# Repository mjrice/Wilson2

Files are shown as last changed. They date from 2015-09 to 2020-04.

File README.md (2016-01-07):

# Wilson2

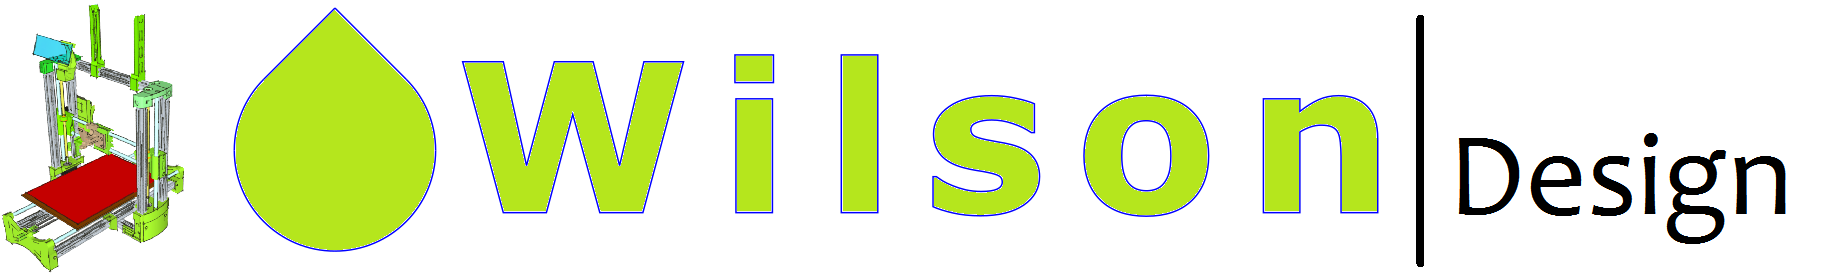
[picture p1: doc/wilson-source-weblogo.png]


This is the design repository for the Wilson II - a reprap 3D printer based on Wilson TS, inspired by the Prusa i3 and the Lulzbot TAZ.

The respository has these sub directories:

    stl/ contains the STL files needed to build the printer
    doc/ contains documentation, images, bom, etc.
    scad/ contains the design files of those parts for which OpenSCAD was used.
    sketchup/ contains the design files of those parts for which SketchUp was used.

There is also a community forum for this project, located at http://community.reprapwilson3d.com

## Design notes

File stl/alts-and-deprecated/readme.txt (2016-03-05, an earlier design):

/stl/alts-and-deprecated

The model files located in this folder are for 
rarely used alternate versions of some parts, or
deprecated models (things no longer recommended 
for the standard Wilson II build).

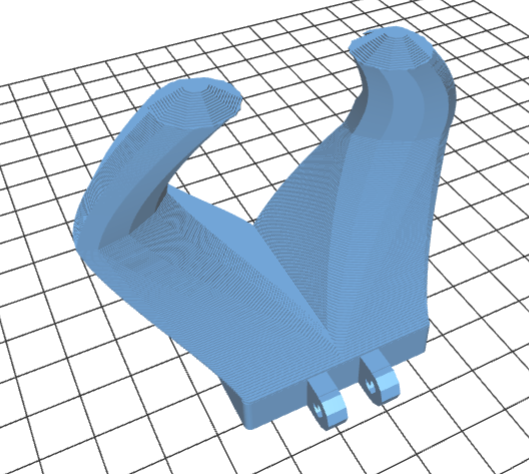
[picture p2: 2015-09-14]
doc/fanduct-e3dlite6.png

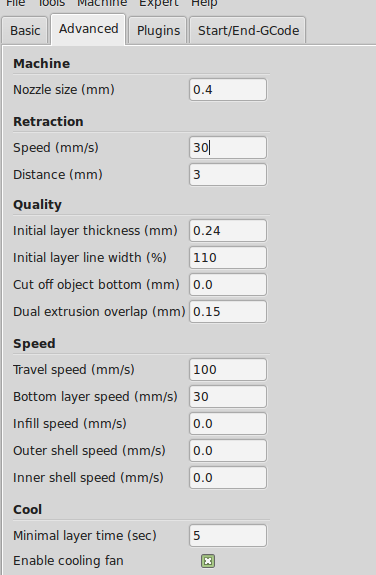
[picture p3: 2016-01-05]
doc/cura2.png

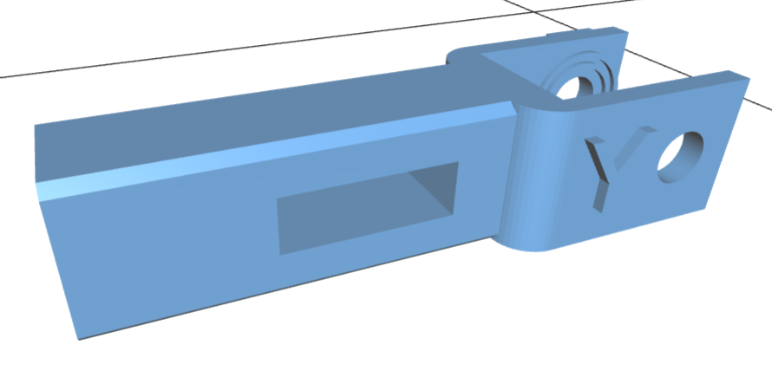
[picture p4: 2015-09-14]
doc/y-tensioner.png

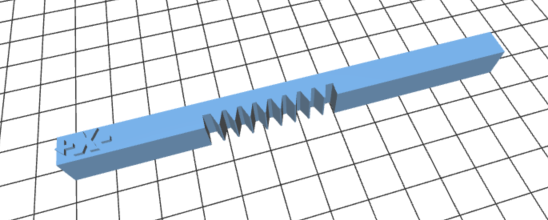
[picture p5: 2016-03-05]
doc/z-rack.png

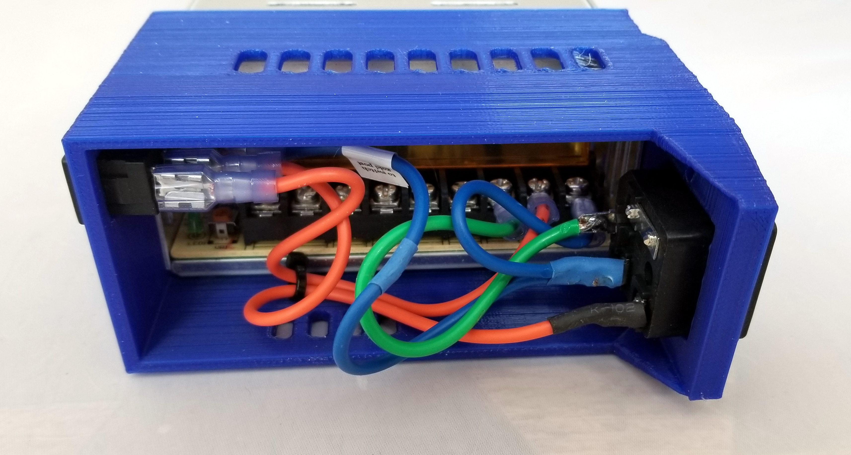
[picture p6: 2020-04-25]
doc/power-inlet-detail-assy.jpg

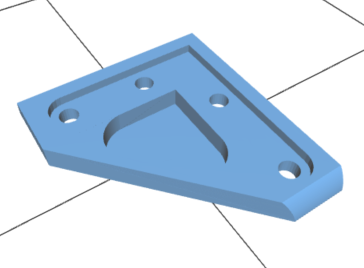
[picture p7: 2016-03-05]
doc/z-lower-brace-2.png

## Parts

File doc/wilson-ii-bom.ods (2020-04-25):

Reprap Wilson II Parametric build parts list
 | Set these values:
Unit system: | metric | ← Enter “metric” or “sae” here
Build variation: | II
Desired print width (X): | 200 | mm
Desired print depth (Y): | 300 | mm
Desired print height (Z): | 200 | mm
Item | Quantity | Length / Notes
2020 Extrusions
Vertical frame piece (sides) | 4 | 400 | mm | 400
Horizontal frame piece (top and bottom) | 3 | 330 | mm | 330
Y axis frame piece | 2 | 500 | mm | 500
M10 Smooth Rods
X-Axis | 2 | 370 | mm | 370 | +/- 10 mm is ok
Y-Axis | 2 | 500 | mm | 500 | precise!
Z-Axis | 2 | 320 | mm | 320 | +/- a few mm is ok
Threaded Rods
8mm lead screw | 2 | 300 | mm |  | like THSL-300-8D
Belts & Pulleys
Y axis GT2 timing belt (w=6mm) | 1 | 1030 | mm | 1030
X axis GT2 timing belt (w=6mm) | 1 | 900 | mm
GT2 pulley | 2 | Want diameter 16-20mm
Nuts & Bolts
M5 x 10mm machine screw | 55
M5 t slot nut | 55
M4 x 10mm machine screw | 4 | These are used for the psu mounting bracket
M4 x 20mm machine screw | 4 | For belt idlers and tensioners
M4 x 25mm machine screw | 4 | These are used to mount the extruder to the X carriage
M4 hex nut | 6
M4 lock nut | 2 | Use for idler bearing assemblies
M3 x 10mm machine screw | 12 | Z and Y axis motor mounts
M3 x 14mm machine screw | 19 | 3 for X motor, 4 for extruder fan, 2 for lcd mount, 4 for lead screw nut mounts, 2 for ramps cooling fan, for for y table
M3 x 25mm machine screw | 6 | 3 for extruder stepper motor, 1 for fan duct to the extruder, 2 for tensioners
M3 x 30mm machine screw | 6 | 4 for print bed, 2 for hot end clamp / servo mount
M3 x 60mm machine screw | 2 | These are used for the extruder
M3 hex nut | 22
M3 lock nut | 5 | use locknuts for print bed mount and fan duct mount
M3 washer | 10 | Need 4 for extruder springs, but have some handy if needed elsewhere
M2 x 16mm machine screw | 9 | These and M2 nuts for mounting end stops, 1 for servo mount, and 2 for LM2596 mount
M2 hex nut | 9
Printed Parts – Required
X end idler | 1 | X-end-idler.stl
X end motor | 1 | X-end-motor.stl
X carriage | 1 | X-carriage.stl
X belt tensioner | 1 | X-tensioner.stl
Y end idler | 1 | Y-idler.stl
Y belt tensioner | 1 | Y-tensioner.stl
Y end motor | 1 | Y-motor.stl
Y table mount | 1 | Y-table-10.stl
Z motor holder, left | 1 | Z-motor-left.stl
Z motor holder, right | 1 | Z-motor-right.stl
Z top frame, left | 1 | Z-top-left.stl
Z top frame, right | 1 | Z-top-right.stl
Z lower corner brace, front/right, back/left | 2 | Z-lower-brace-1.stl
Z lower corner brace, front/left, back/right | 2 | Z-lower-brace-2.stl
Y frame brace | 4 | Y-brace.stl
Idler bearing guide (two parts makes one guide) | 4 | Belt-guide-624.stl
Extruder body / idler / hot end clamp set | 1 | Extruder-direct-drive.stl
Servo mount | 1 | servo_mount.stl
Servo endstop mount | 1 | Servo-endstop-holder.stl
Extruder fan duct | 1 | Fanduct-e3dlite6.stl
Printed Parts – Recommended
Electronics frame mount (for RAMPS) | 1 | Ramps-mount.stl
Filament spool support (two pieces) | 1 | Filament-mount.stl
SMART display frame mount (one piece) | 1 | Smartlcd-mount.stl
12V PSU frame mounting bracket | 2 | Psu-mount.stl
Power switch mount | 1 | Power-switch-mount.stl
Everything Else
NEMA17 Stepper motor | 5 | 4-wire bipolar, high torque preferrably
MDF board (heated bed mount) | 1 | see drawing for board in doc/
Heat bed PCB | 1 | 200x300mm MK1
Heat bed thermistor | 1
Glass bed | 1 | 3mm borosilicate or picture frame glass
Controller (Mega/RAMPS, Rambo, etc) | 1 | Arduino Mega 2560 + RAMPS + A4988 drivers * 4
SMART lcd controller / SD reader | 1
Endstop (limit) switch | 3 | 6mm x 10mm x 20mm, “snap action” levered switch
Micro servo (9g type) | 1 | add wire to make ~ 70cm
LM10UU linear bearing | 12
608ZZ roller bearing | 2 | these go in the z tops to hold the upper end of the lead screws (ok if you don't have them)
624RS roller bearing | 3 | one for each belt idler, one for extruder
MK7 Drive gear (or similar) | 1
Brass or delrin lead screw nut | 2 | Probably comes with your lead screws?
5mm to 8mm flexible shaft couplers | 2 | aluminum
40mm x 40mm x 10mm fan | 1 | 12V
80mm x 80mm x 10mm fan | 1 | For use with RAMPS frame mount
Miniature zip ties | 20 | This number is approximate
Extruder idler springs | 2 | High tension, 1” unsprung length, >3mm ID
Bed leveling springs | 4 | Lower tension is OK, 1” unsprung, ID > 3mm
Power Supply | 1 | Size appropriately for heat bed and extruder
Hot end | 1 | E3d lite6 or E3d v6
Power switch | 1 | KCD1-104N (12mm x 19mm body)
Tools you'll probably need
Phillips screwdriver
Small flat head screwdriver
Metric ruler
13mm wrench
Wire cutters
Small metal (diamond) files | For cleaning up printed parts
Drill
3mm, 5mm, 8mm drill bits | Or 9/64”, 13/64”, and 5/16”
Allen wrenches | If using socket-cap screws for frame, and for pulleys
Pliers
Soldering iron
Kapton tape (polyimide)
Notes about wires
The lengths shown are conservative estimates to help you plan for what you'll need
Extruder heater wire pair | 70cm
Extruder thermistor wire pair | 70cm
Extruder fan wire pair | 70cm
X end stop wire pair | 25cm
Y end stop wire pair | 50cm
Z end stop wire pair | 25cm
X motor wires (4) | 25cm
Y motor wires (4) | 50cm
Z left motor wires (4) | 25cm
Z right motor wires (4) | 60cm
Extruder motor wires (4) | 70cm
Heat bed power wires | 60cm | 12 Gauge or heavier
Heat bed thermistor wires | 50cm

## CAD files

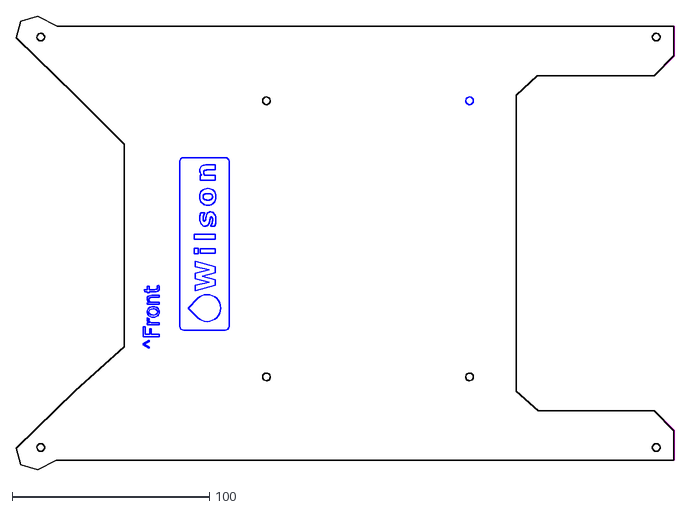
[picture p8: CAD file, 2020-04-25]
doc/wilson-bed-2030-lc.dxf
333.6 x 230.0

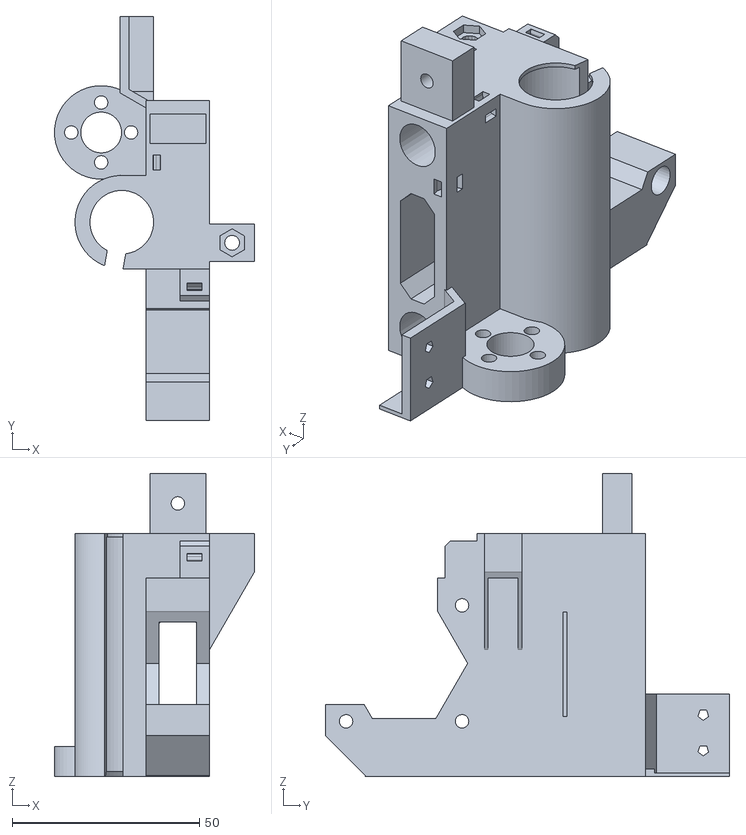
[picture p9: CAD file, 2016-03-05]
scad/motor.stl
53.5 x 108.0 x 81.0

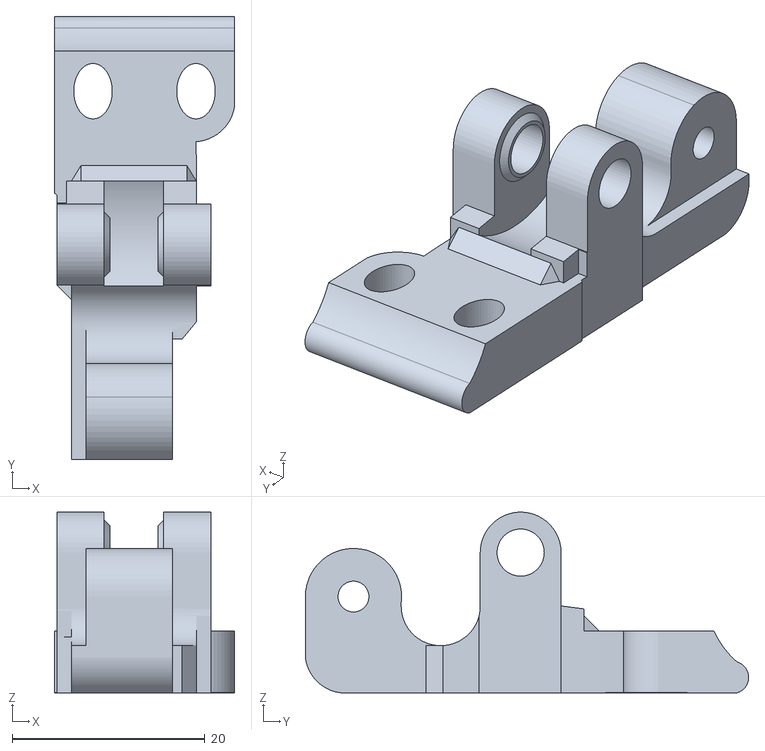
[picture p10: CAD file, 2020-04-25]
stl/extruder_idler.stl
18.7 x 46.1 x 18.8

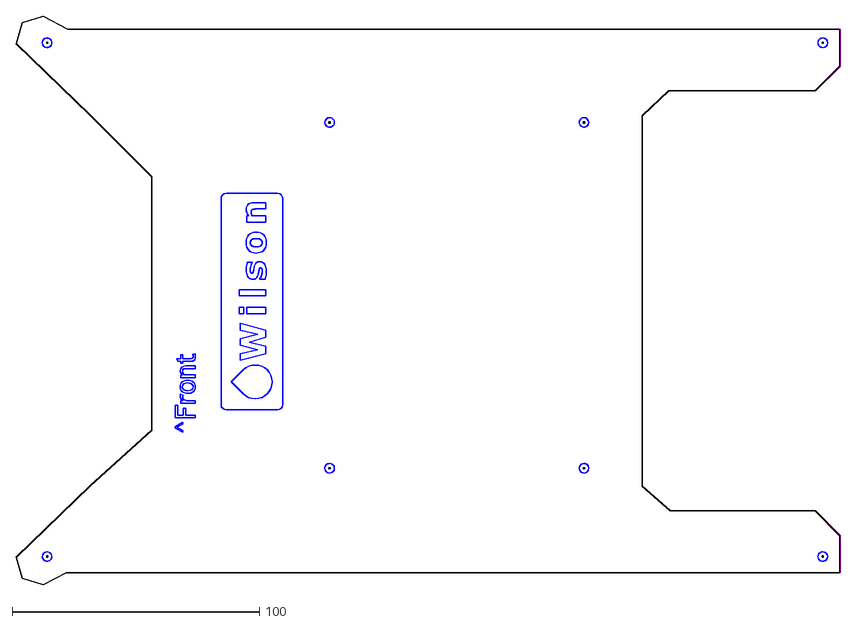
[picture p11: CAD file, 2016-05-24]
doc/wilson-bed-2030-lc-2pass.dxf
333.6 x 230.0

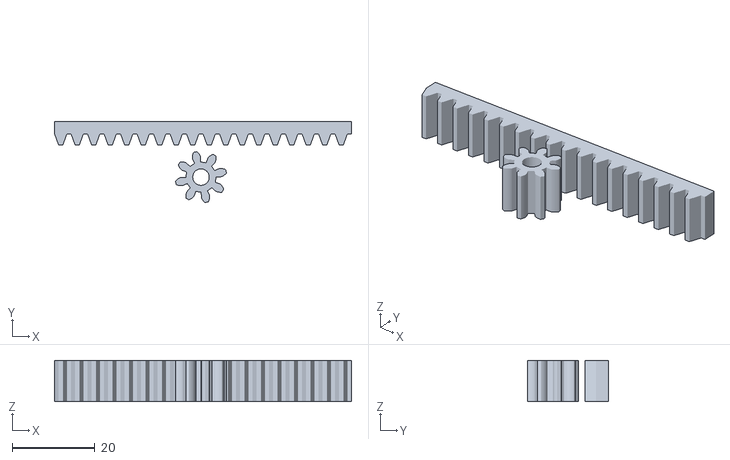
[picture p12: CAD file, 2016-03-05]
scad/rack_and_pinion.stl
72.0 x 19.7 x 10.0

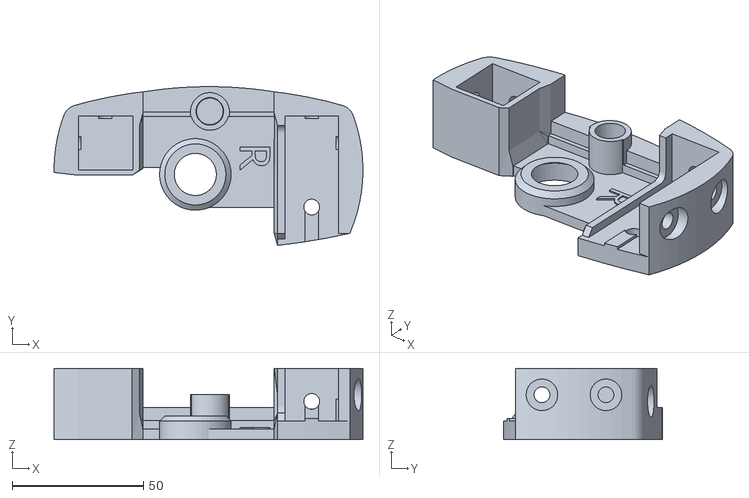
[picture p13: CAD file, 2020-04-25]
stl/z-top-right.stl
117.5 x 60.4 x 27.0

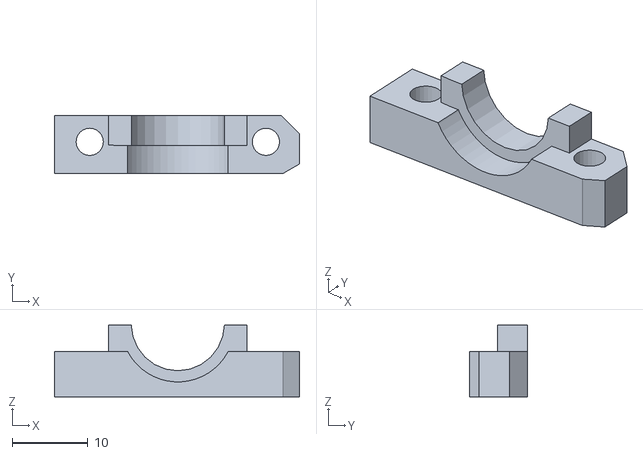
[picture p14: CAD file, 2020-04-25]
stl/extruder-clamp.stl
32.4 x 7.70 x 9.46

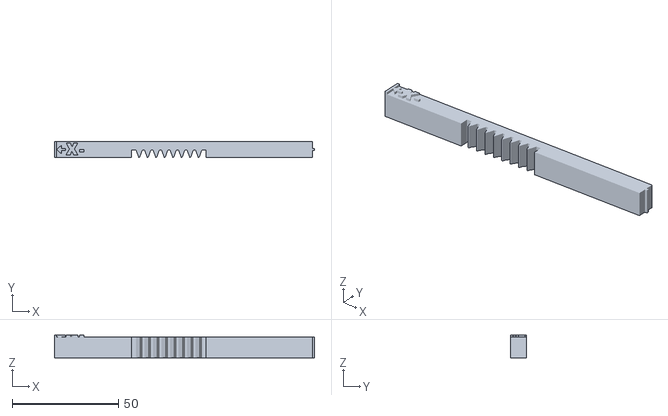
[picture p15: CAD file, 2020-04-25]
stl/z-rack.stl
122.3 x 7.67 x 10.8

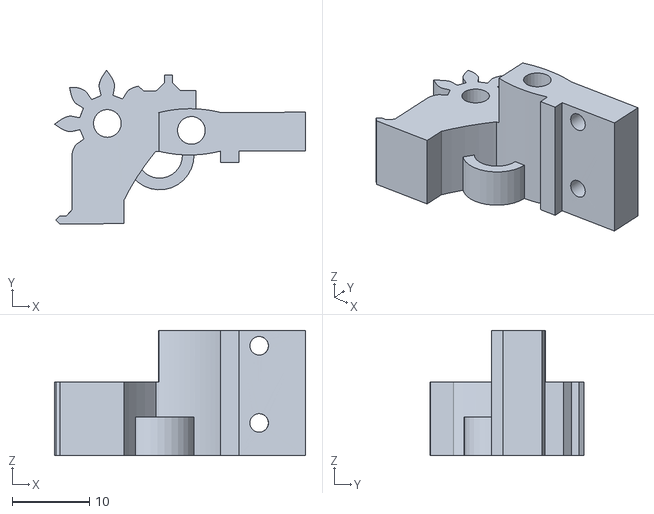
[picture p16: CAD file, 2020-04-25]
stl/z-pinion.stl
32.5 x 19.9 x 16.2

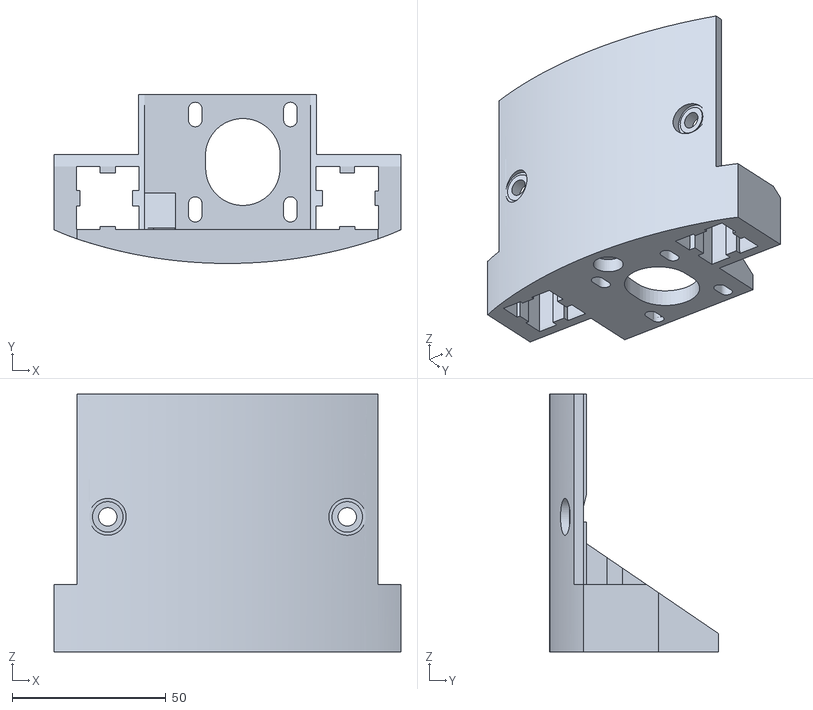
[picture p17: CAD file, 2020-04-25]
stl/z-motor-right.stl
113.0 x 55.0 x 84.0

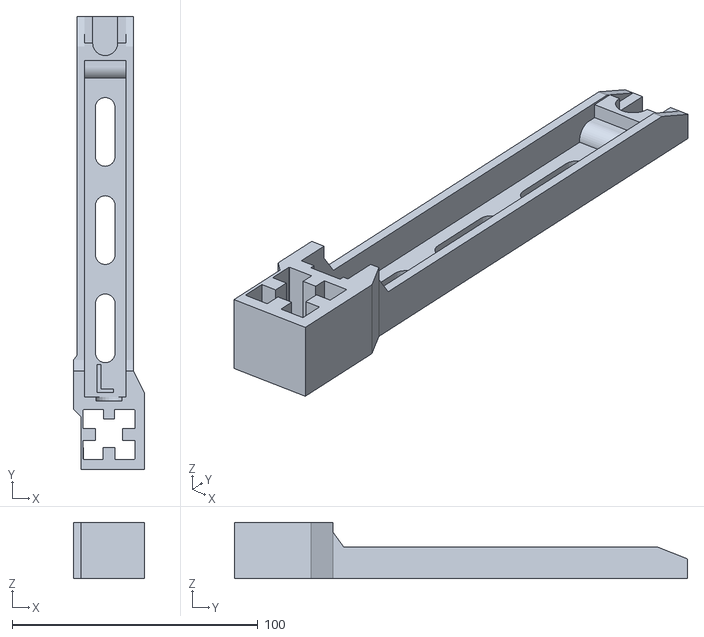
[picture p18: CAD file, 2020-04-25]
stl/filament_mount_left.stl
29.0 x 184.5 x 22.9

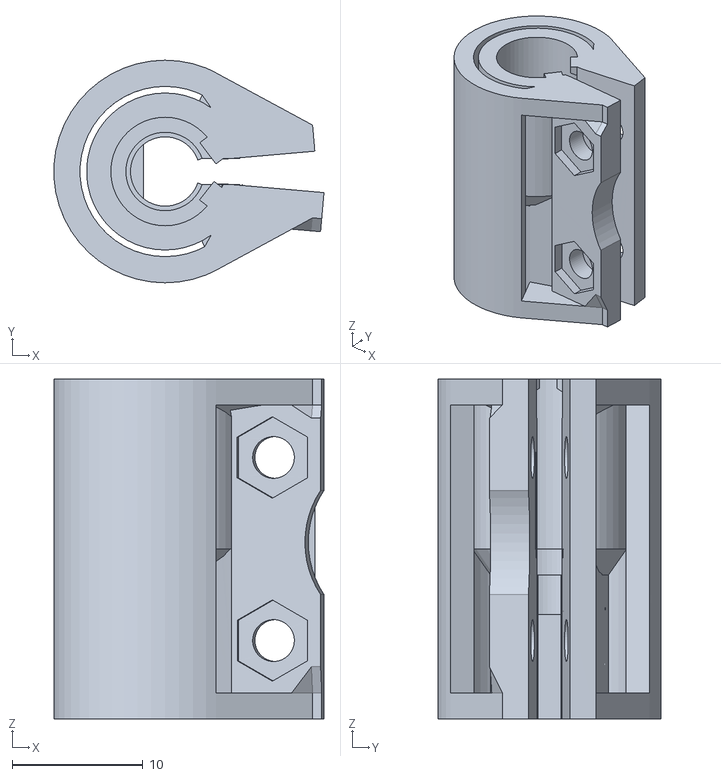
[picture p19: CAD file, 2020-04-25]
stl/coupler-5x8.stl
20.6 x 17.0 x 26.0

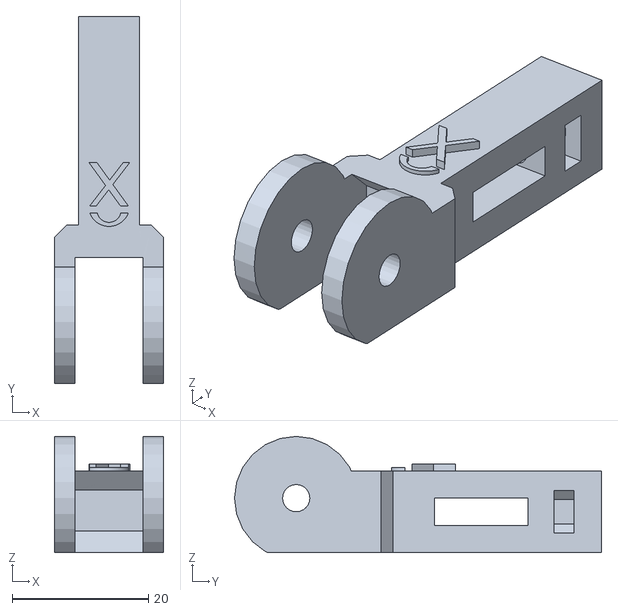
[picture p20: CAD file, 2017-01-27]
stl/x-tensioner.stl
16.0 x 53.9 x 17.1

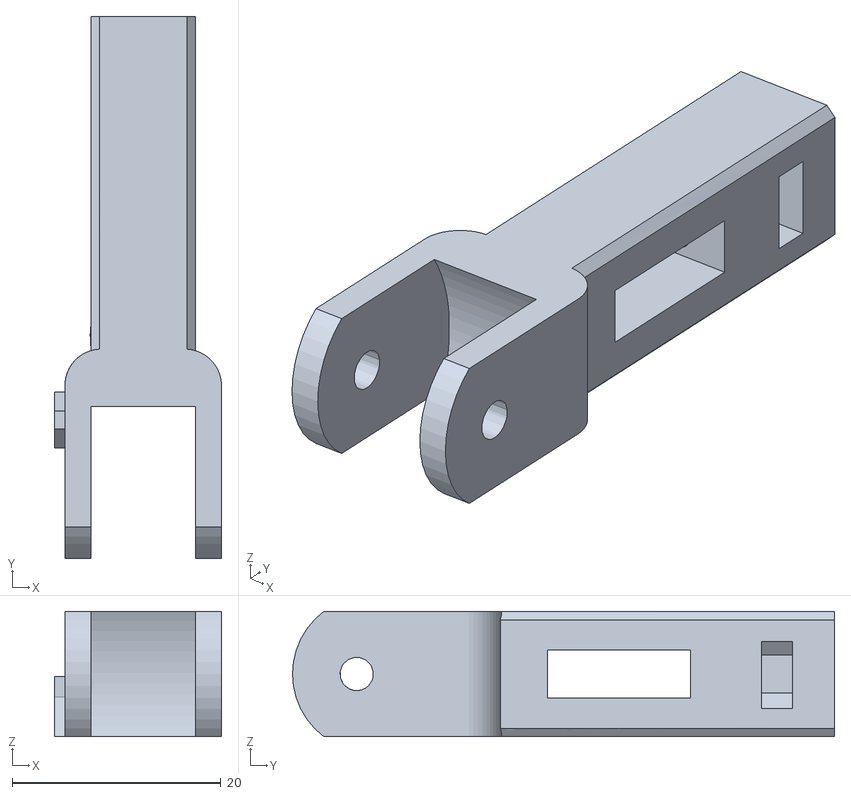
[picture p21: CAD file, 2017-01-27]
stl/y-tensioner.stl
16.0 x 52.0 x 12.0

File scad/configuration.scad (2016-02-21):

smooth_rod_d      = 10; //8
threaded_rod_d    = 8; //10?
tie_wrap_w        = 5;
tie_wrap_t        = 2;
washer_d          = 21;
height_of_threaded = 26.5;
height_of_smooth = height_of_threaded + 11 + 9;
height_of_post = height_of_smooth+2;

belt_width = 6.5;
belt_tooth_distance = 2;
belt_tooth_ratio = 0.5;
belt_thickness = 0.8;

idler_bearing_inner_d = 4; // 624 bearing

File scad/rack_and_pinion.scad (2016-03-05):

// Rack and pinion gears GPL (c) SASA October 2013.
//
// Very simple rack and pinion gear based on GPL code.
//
// I've made corrections to both rack and gear code I used (below) and unified
// and simplified both bits of code.  Corrects the use of circular pitch so
// rack and pinion match nicely.  Ammendments to the code and interface to
// simplify use and improve readability. Many bells and whistles dropped in
// favour of being dead simple.  I also opted for hard wiring the pressure
// angle to 20 degrees since this seemed a kind of standard.
//
// Based on the works (thanks!): Parametric Involute Bevel and Spur Gears by
// GregFrost GNU GPL license.  http://www.thingiverse.com/thing:3575 Parametric
// Modular Rack by Mark "Ckaos" Moissette GNU GPL license.  (Rack based on the
// work of MattMoses and Fdavies
// http://forums.reprap.org/read.php?1,51452,52099#msg-52099 and Forrest Higgs:
// 
// The originals have many fine additions such as helical gears which I've
// dropped in favour of simplicity (as befits my needs) - it wouldn't be a big
// jobs to nobble my changes backwards or their features forwards.

pi=3.1415926535897932384626433832795;
$fn=50;

// examples of usage
// include this in your code:
// use <rack_and_pinion.scad>
// then:
// a simple rack
// rack(4,20,10,1);//CP (mm/tooth), width (teeth), thickness(of base) (mm), # teeth
// a simple pinion and translation / rotation to make it mesh the rack
// translate([0,-8.5,0])rotate([0,0,360/10/2]) pinion(4,10,10,5);


rack (4,18,10,3);

translate([0,-12,0]) rotate([0,0,13]) pinion(4,8,10,4);


module rack(cp, N, width, thickness){
// cp = circular pitch - for rack = pitch in mm/per tooth
// N = number of teeth
// width = width of rack in teeth
// thickness = thickness of support under teeth (0 for no support)

	a = 1.0*cp/pi; // addendum (also known as "module")
	d = 1.1*cp/pi; // dedendum (this is set by a standard)
	height=(d+a);

	// find the tangent of pressure angle once
	tanPA = tan(20);
	// length of bottom and top horizontal segments of tooth profile
	botL = (cp/2 - 2*d*tanPA);
	topL = (cp/2 - 2*a*tanPA);

	slantLng=tanPA*height;
	realBase=2*slantLng+topL;

	offset=topL+botL+2*slantLng;
	length=(realBase+botL)*N;

	supportSize=width;
	translate([botL/2,0,0])
	rotate([90,0,0]){
		translate([0,supportSize/2,0]){
			union(){
				cube(size=[length,width,thickness],center=true);
				for (i = [0:N-1]){
					translate([i*offset-length/2+realBase/2,0,thickness/2]){
						trapezoid([topL,supportSize],[realBase,supportSize],height);
						}
					}
				}
			}
		}
	}

module pinion (cp, N, width, shaft_diameter, backlash=0){
// cp= circular pitch - for pinion pitch in mm/per as measured along the ptich radius (~1/2 way up tooth)
// N= number of teeth
// width= width of the gear
// shaft_diameter= diameter of hole for shaft
// backlash - I think this is just a bodge for making things fit when printed but I never tested it

	if (cp==false && diametral_pitch==false) 
		echo("MCAD ERROR: pinion module needs either a diametral_pitch or cp");

	//Convert diametrial pitch to our native circular pitch
	cp = (cp!=false?cp:180/diametral_pitch);

	// Pitch diameter: Diameter of pitch circle.
	pitch_diameter  =  N * cp / pi;
	pitch_radius = pitch_diameter/2;
	echo ("Teeth:", N, " Pitch radius:", pitch_radius);
	// Base Circle
	base_radius = pitch_radius*cos(20);

	// Addendum: Radial distance from pitch circle to outside circle.
	addendum = cp/pi;

	//Outer Circle
	outer_radius = pitch_radius+addendum;

	// Dedendum: Radial distance from pitch circle to root diameter
	dedendum = addendum*1.1;

	// Root diameter: Diameter of bottom of tooth spaces.
	root_radius = pitch_radius-dedendum;

	backlash_angle = backlash / pitch_radius * 180 / pi;
	half_thick_angle = (360 / N - backlash_angle) / 4;

	difference(){
		linear_extrude (height=width, convexity=10, twist=0)
		pinion_shape(N, pitch_radius = pitch_radius, root_radius = root_radius,
			base_radius = base_radius, outer_radius = outer_radius,
			half_thick_angle = half_thick_angle, involute_facets=0);

		translate([0,0,-1]) cylinder(r=shaft_diameter/2,h=2+width);
		}

	echo("Root radius =",root_radius,"\nPitch radius=",pitch_radius,"\n Tip radius=",outer_radius,"\n");
	}

module pinion_shape ( N, pitch_radius, root_radius, base_radius, outer_radius, half_thick_angle, involute_facets) {
	union(){
		rotate (half_thick_angle) circle ($fn=N*2, r=root_radius);
		for (i = [1:N]) {
			rotate ([0,0,i*360/N]) {
				involute_pinion_tooth (
					pitch_radius = pitch_radius,
					root_radius = root_radius,
					base_radius = base_radius,
					outer_radius = outer_radius,
					half_thick_angle = half_thick_angle,
					involute_facets=involute_facets);
				}
			}
		}
	}

module involute_pinion_tooth ( pitch_radius, root_radius, base_radius, outer_radius, half_thick_angle, involute_facets) {
	min_radius = max (base_radius,root_radius);

	pitch_point = involute (base_radius, involute_intersect_angle (base_radius, pitch_radius));
	pitch_angle = atan2 (pitch_point[1], pitch_point[0]);
	centre_angle = pitch_angle + half_thick_angle;

	start_angle = involute_intersect_angle (base_radius, min_radius);
	stop_angle = involute_intersect_angle (base_radius, outer_radius);

	res=(involute_facets!=0)?involute_facets:($fn==0)?5:$fn/4;

	union () {
		for (i=[1:res])
		assign ( point1=involute (base_radius,start_angle+(stop_angle - start_angle)*(i-1)/res), point2=involute (base_radius,start_angle+(stop_angle - start_angle)*i/res)) {
			assign (
				side1_point1=rotate_point (centre_angle, point1),
				side1_point2=rotate_point (centre_angle, point2),
				side2_point1=mirror_point (rotate_point (centre_angle, point1)),
				side2_point2=mirror_point (rotate_point (centre_angle, point2))) {
				polygon ( points=[[0,0],side1_point1,side1_point2,side2_point2,side2_point1], paths=[[0,1,2,3,4,0]]);
				}
			}
		}
	}

// Mathematical Functions
//===============

// Finds the angle of the involute about the base radius at the given distance (radius) from it's center.
//source: http://www.mathhelpforum.com/math-help/geometry/136011-circle-involute-solving-y-any-given-x.html

function involute_intersect_angle (base_radius, radius) = sqrt (pow (radius/base_radius, 2) - 1) * 180 / pi;

// Calculate the involute position for a given base radius and involute angle.

function rotated_involute(rotate,base_radius,involute_angle)=[cos(rotate)*involute(base_radius, involute_angle)[0]+sin(rotate)*involute(base_radius, involute_angle)[1],cos(rotate)*involute(base_radius, involute_angle)[1]-sin(rotate)*involute(base_radius, involute_angle)[0]];

function mirror_point(coord)=[coord[0],-coord[1]];

function rotate_point(rotate,coord)=[cos(rotate)*coord[0]+sin(rotate)*coord[1],cos(rotate)*coord[1]-sin(rotate)*coord[0]];

function involute (base_radius, involute_angle)=[base_radius*(cos(involute_angle)+involute_angle*pi/180*sin(involute_angle)),base_radius*(sin(involute_angle)-involute_angle*pi/180*cos(involute_angle))];




module trapezoid(top,base,height){
	//echo ("test",base[0]);
	basePT1=[ -base[0]/2, base[1]/2, 0];
	basePT2=[ base[0]/2, base[1]/2, 0];
	basePT3=[ base[0]/2, -base[1]/2, 0];
	basePT4=[ -base[0]/2, -base[1]/2, 0];
	topPT1=[ -top[0]/2, top[1]/2, height];
	topPT2=[ top[0]/2, top[1]/2, height];
	topPT3=[ top[0]/2, -top[1]/2, height];
	topPT4=[ -top[0]/2, -top[1]/2, height];
	polyhedron(points=[ basePT1, basePT2, basePT3, basePT4, topPT1, topPT2, topPT3, topPT4],triangles=[[0,1,2], [0,2,3],[3,7,0], [7,4,0],[1,6,2], [1,5,6],[2,6,3], [3,6,7],[5,1,0],[4,5,0],[7,5,4],[5,7,6]]);
	}

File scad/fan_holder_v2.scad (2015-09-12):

/*
OPENSCAD Library file by the DoomMeister
Mounting surround for small DC fans (25 - 120mm)

Data taken from various places around the internet.
http://www.qwikflow.com/dc_fans.html

//Released under the terms of the GNU GPL v3.0
This program is free software: you can redistribute it and/or modify
it under the terms of the GNU General Public License as published by
the Free Software Foundation, either version 3 of the License, or
(at your option) any later version.

This program is distributed in the hope that it will be useful,
but WITHOUT ANY WARRANTY; without even the implied warranty of
MERCHANTABILITY or FITNESS FOR A PARTICULAR PURPOSE. See the
GNU General Public License for more details.

You should have received a copy of the GNU General Public License
along with this program. If not, see <http://www.gnu.org/licenses/>.
*/

//uncomment this for example
fan_mount(size=40,thick=3);

module fan_mount(size=40,thick = 4)
{
if(size == 25)
	{
	_fan_mount(
			fan_size = 25,
			fan_mounting_pitch = 20,
			fan_m_hole_dia = 3,
			holder_thickness = thick
		 );
	}
if(size == 30)
	{
	_fan_mount(
			fan_size = 30,
			fan_mounting_pitch = 24,
			fan_m_hole_dia = 3,
			holder_thickness = thick
		 );
	}

if(size == 40)
	{
	_fan_mount(
			fan_size = 40,
			fan_mounting_pitch = 32,
			fan_m_hole_dia = 3.7,
			holder_thickness = thick
		 );
	}
if(size == 45)
	{
	_fan_mount(
			fan_size = 45,
			fan_mounting_pitch = 37,
			fan_m_hole_dia = 4.3,
			holder_thickness = thick
		 );
	}
if(size == 60)
	{
	_fan_mount(
			fan_size = 60,
			fan_mounting_pitch = 50,
			fan_m_hole_dia = 4.4,
			holder_thickness = thick
		 );
	}
if(size == 80)
	{
	_fan_mount(
			fan_size = 80,
			fan_mounting_pitch = 71.5,
			fan_m_hole_dia = 4.4,
			holder_thickness = thick
		 );
	}

if(size == 120)
	{
	_fan_mount(
			fan_size = 120,
			fan_mounting_pitch = 105,
			fan_m_hole_dia = 4.4,
			holder_thickness = thick
		 );
	}
}


//inner module
module _fan_mount(
			fan_size, //nominsl size of fan
			fan_mounting_pitch, //pitch between mounting holes
			fan_m_hole_dia, //mounting hole diameter
			holder_thickness //user defined thickness
		 )
{

offset1 = (fan_size-(fan_mounting_pitch + fan_m_hole_dia))/2;
offset2 = (fan_size-(fan_mounting_pitch))/2;
offset3 = offset2 + fan_mounting_pitch;
thickness = (fan_size-fan_mounting_pitch)/2;	
			
			//difference()
			//{
			linear_extrude(height = holder_thickness)
			union()
			{	
			difference()
			{
				translate([fan_m_hole_dia/2,fan_m_hole_dia/2,0])
				minkowski()
				{	
					square([fan_size - fan_m_hole_dia,fan_size - fan_m_hole_dia]);
					circle(r= fan_m_hole_dia/2, $fn=20);
				}
			
					translate([offset1,offset1,0])
					square([fan_mounting_pitch + fan_m_hole_dia,fan_mounting_pitch + fan_m_hole_dia]);
				}
				translate([offset2,offset2,0])
				rotate([0,0,0])_corner_hole();
				translate([offset3,offset2,0])
				rotate([0,0,90])_corner_hole();
				translate([offset2,offset3,0])
				rotate([0,0,90])_corner_hole();
				translate([offset3,offset3,0])
				rotate([0,0,0])_corner_hole();
			}

module _corner_hole()
{
				difference(){
					union(){
							difference(){
							square([fan_m_hole_dia + thickness,fan_m_hole_dia + thickness],center=true);
							square([(fan_m_hole_dia + thickness)/2,(fan_m_hole_dia + thickness)/2],center=false);
							translate([-(fan_m_hole_dia + thickness)/2,-(fan_m_hole_dia + thickness)/2])
							square([(fan_m_hole_dia + thickness)/2,(fan_m_hole_dia + thickness)/2],center=false);
							}
					circle(r=(fan_m_hole_dia + thickness)/2, $fn=20);
					}
					circle(r=(fan_m_hole_dia)/2, $fn=20);
				}
}


echo(offset1,offset2,thickness);
}

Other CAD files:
stl/z-top-left.stl
stl/z-motor-left.stl
stl/y-idler.stl
stl/y-table-10.stl
scad/FanductOvalE3dv6.scad
scad/pica_mount.scad
scad/shapes.scad
scad/x-end.scad
sketchup/coupler-5x8.skp
sketchup/extruder-direct-drive.skp
sketchup/extruder_body.skp
sketchup/extruder_clamp.skp
sketchup/extruder_idler.skp
sketchup/filament_mount_left.skp
sketchup/filament_mount_right.skp
sketchup/grouped_etc/old-xend-rack-adapter.skp
sketchup/grouped_etc/psu-mounts.skp
sketchup/grouped_etc/servo_mount.skp
sketchup/grouped_etc/xcarriage-rack-pinion.skp
sketchup/grouped_etc/xy-tensioners-wide.skp
sketchup/grouped_etc/xy-tensioners.skp
sketchup/grouped_etc/z-top-bottom.skp
sketchup/pica-mount.skp
sketchup/psu_mount_bottom.skp
sketchup/psu_mount_top.skp
sketchup/shaft-coupler-5x8.skp
sketchup/smartlcd_mount.skp
sketchup/x_carriage.skp
sketchup/x_tensioner.skp
sketchup/y_brace.skp
sketchup/y_idler.skp
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

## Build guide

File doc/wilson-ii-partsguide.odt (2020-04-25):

Wilson II Printed parts guide

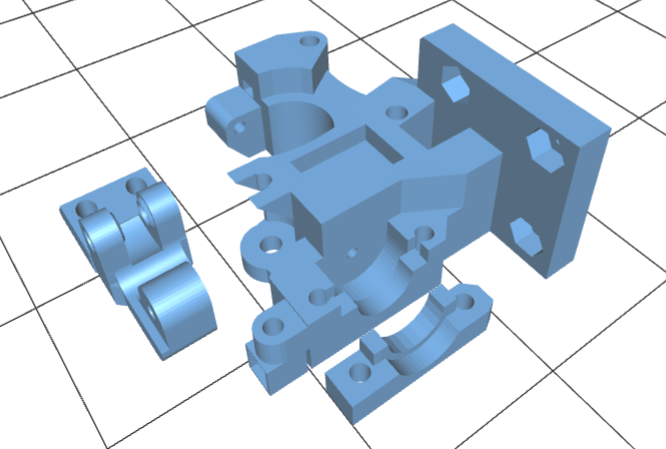
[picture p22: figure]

Extruder-direct-drive.stl (3 pieces)


Fanduct-e3dlite6.stl

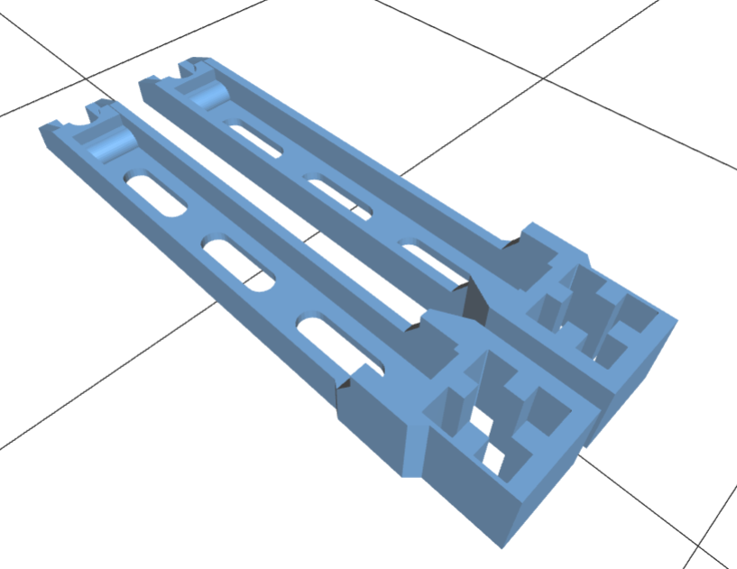
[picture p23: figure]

Filament-mount.stl (2 pieces)

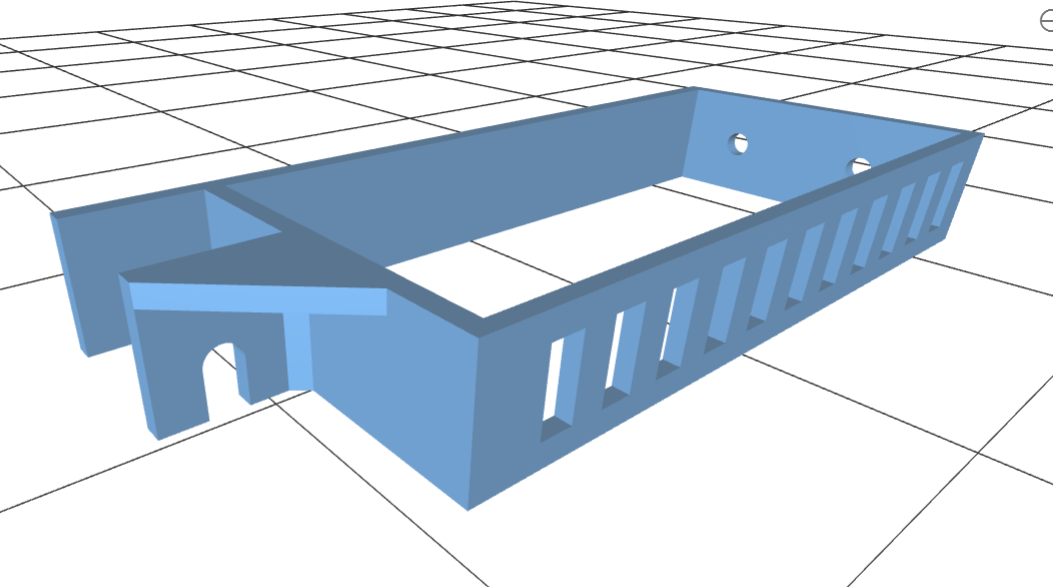
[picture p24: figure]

Psu-mount.stl (1)

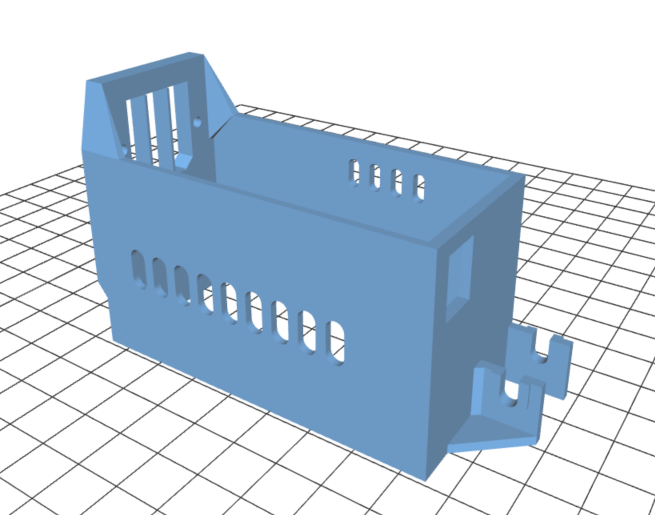
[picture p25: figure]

Psu-mount-bottom.stl (1)

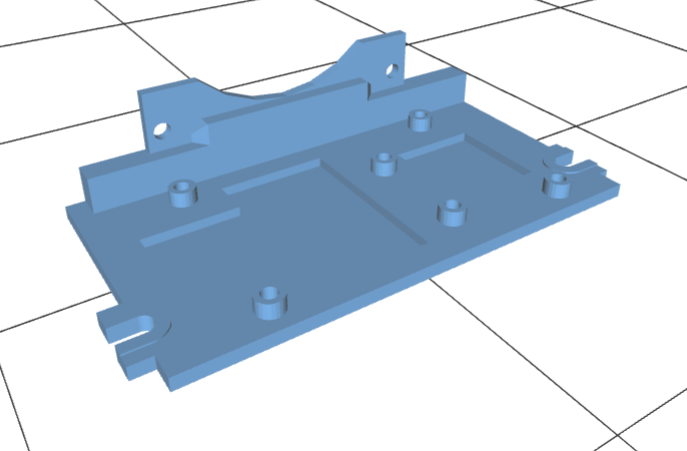
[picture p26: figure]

Ramps-mount.stl (or pica-mount.stl)

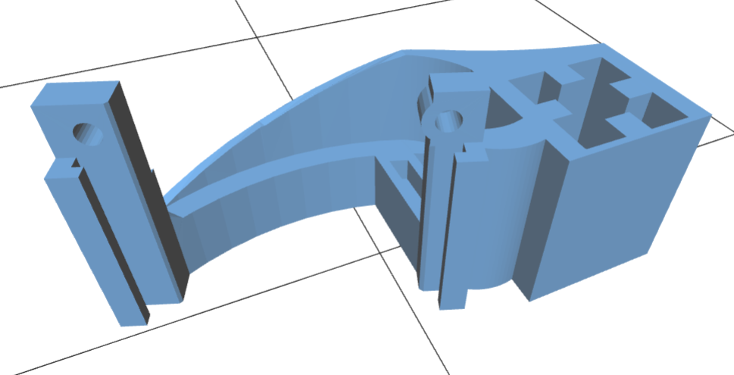
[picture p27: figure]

Smartlcd-mount.stl

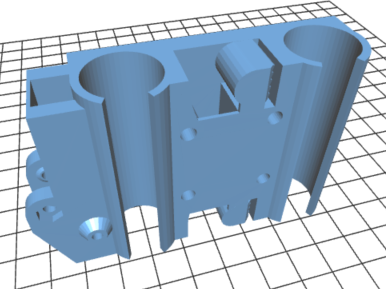
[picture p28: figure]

X-carriage.stl

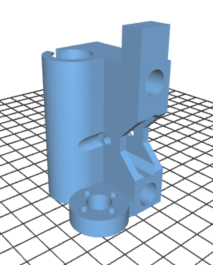
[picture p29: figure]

X-end-idler.stl

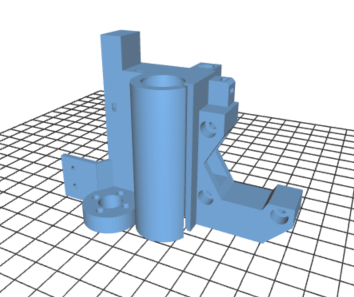
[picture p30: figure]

X-end-motor.stl

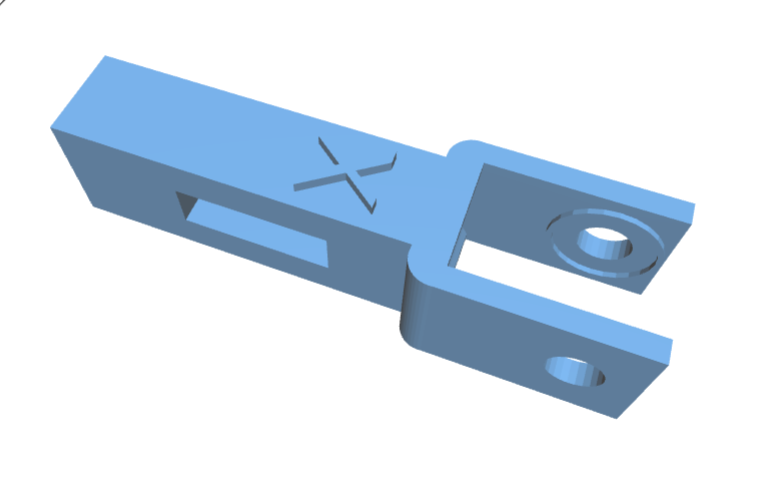
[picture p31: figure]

X-tensioner.stl

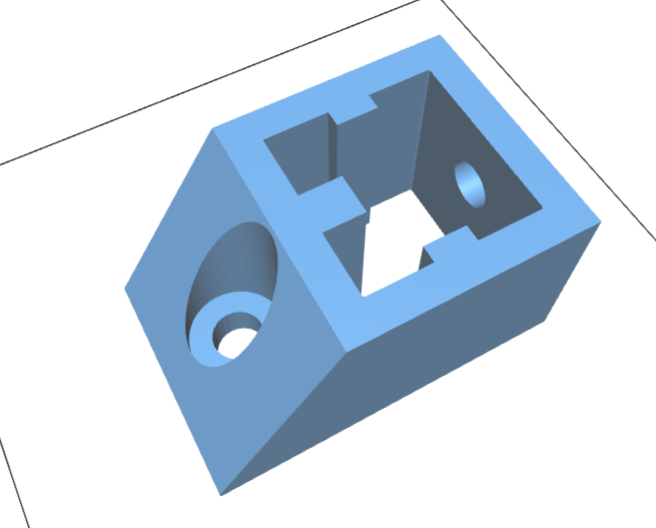
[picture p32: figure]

Y-brace.stl (4)

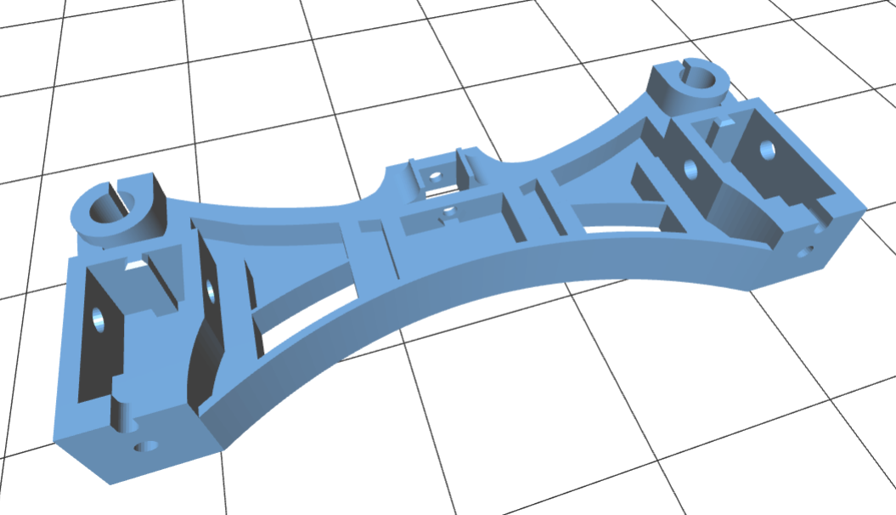
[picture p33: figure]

Y-idler.stl

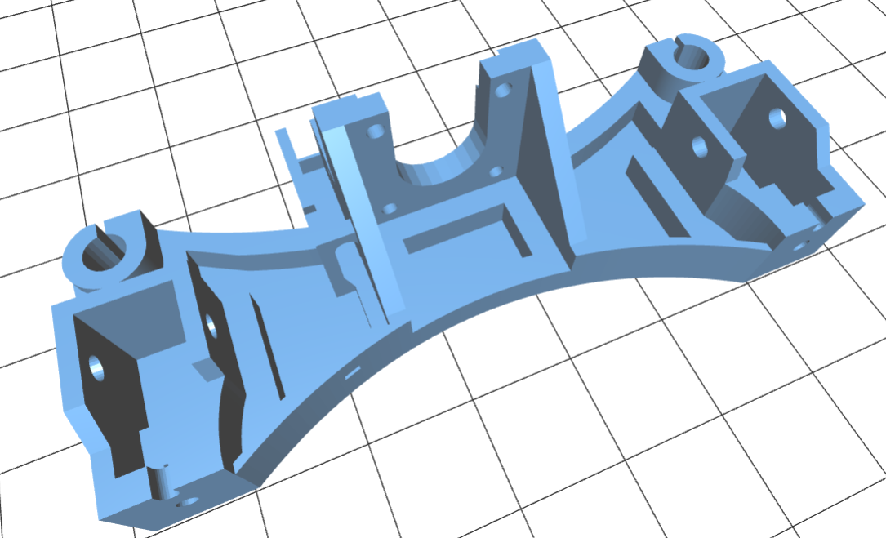
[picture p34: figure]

Y-motor.stl

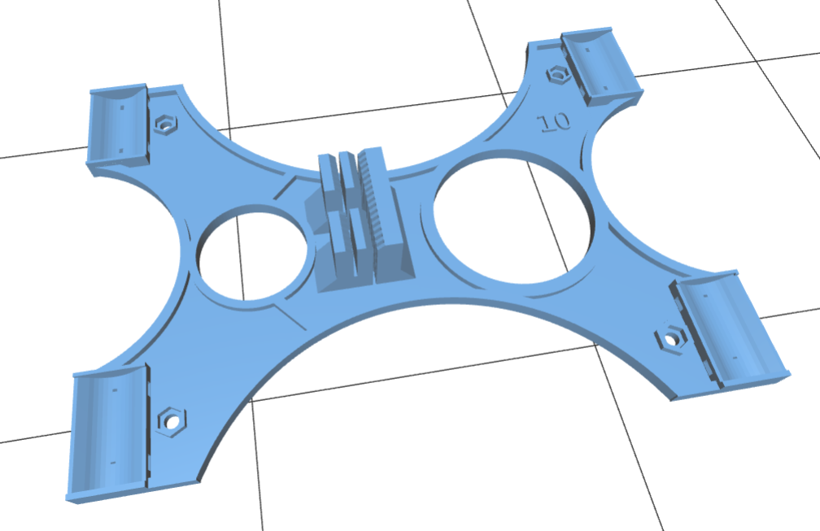
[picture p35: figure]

Y-table-10.stl


Y-tensionersssssswwewewq.stl

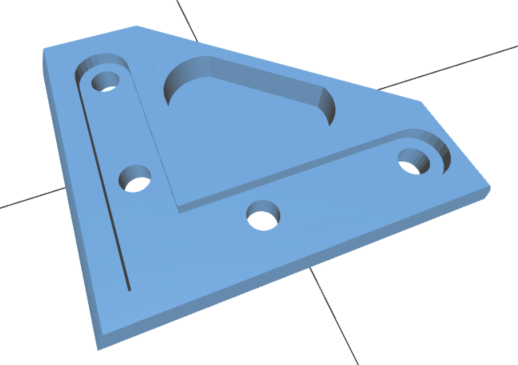
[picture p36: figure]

Z-lower-brace-1.stl (2)


Z-lower-brace-2.stl (2)

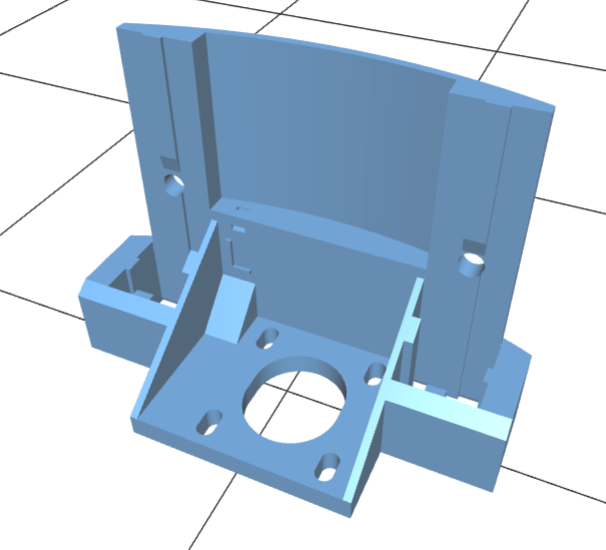
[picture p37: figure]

Z-motor-left.stl

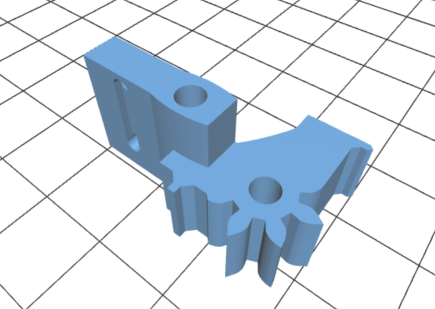
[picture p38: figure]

Z-pinion.stl

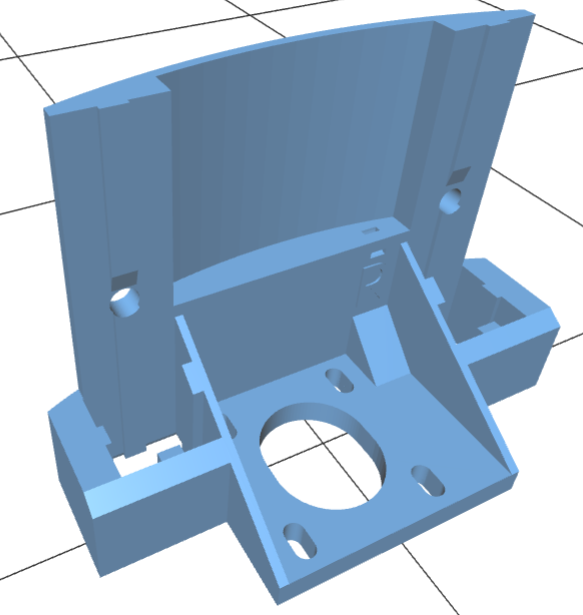
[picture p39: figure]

Z-motor-right.stl

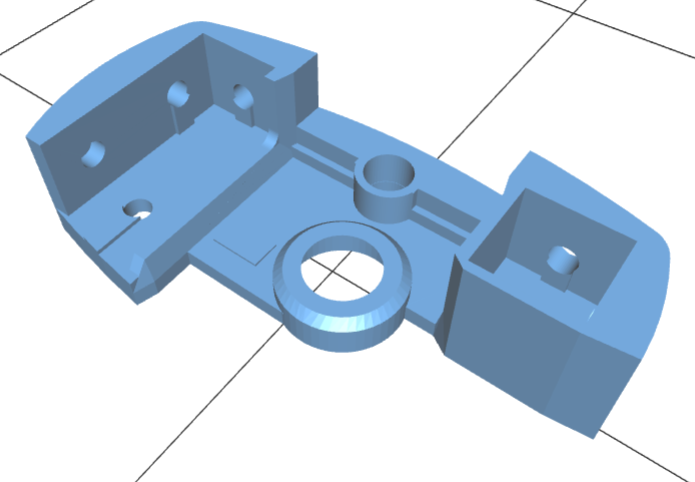
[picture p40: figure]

Z-top-left.stl

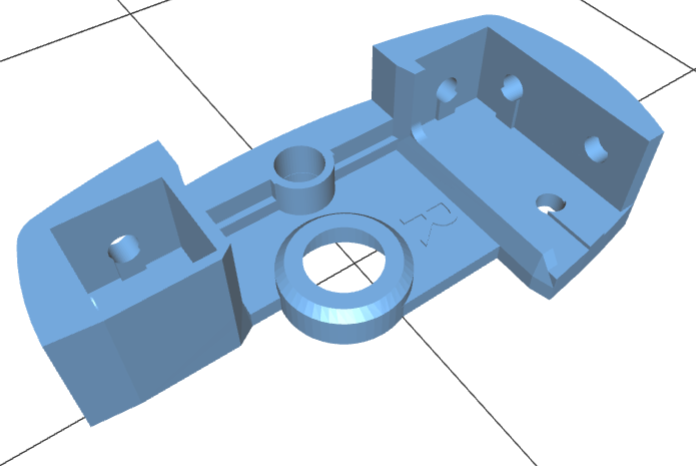
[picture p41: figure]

Z-top-right.stl


Z-rack.stl

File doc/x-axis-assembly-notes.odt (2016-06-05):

# Wilson II X-axis assembly notes

Step by step notes

1. insert the linear bearings into the X ends and X carriage

2. Attach the lead screw nuts to each x end using two M3 x 14mm screws and nuts on each.

3. Assemble the 624 bearing with the printed belt guides and the X tensioner (or use a preassembled idler pulley with the alternate x tensioner) using a M4x20mm screw and hex nut. Insert a M3 nut into the X tensioner and thread M3x30mm screw in just until through nut. Install the X tensioner in the X idler end, using a M4 x 20mm screw to secure the tensioner.

4. Wire each endstop (if not prewired). Z endstop will need about 70cm of wire, the X axis only needs about half that.

5. attach one endstop switch to the X motor end using a miniature zip tie (or two M2 screws and nuts). Secure with a zip tie through the slot provided on the X motor end.

6. Attach one endstop to the Z pinion using a miniaturej zip tie. Secure wires using another zip tie through the small loop provided on the Z pinion to prevent strain on the wire.

7. Slide the Z rack through the slot on the bottom of the X carriage, align the Z pinion, and secure pinion using a M3x20mm screw and hex nut.

8. Attach the extension springs to the Z pinion. On each side of the X carriage, attach an extension spring with a M3x10mm screw into the holes provided. Tighten M3x10mm screws just until bottomed out. Thread a M3x40mm screw through one extension spring, then through the Z pinion, and attach the other extension spring to the other side of the M3x40mm screw. Attach a M3 locknut and tighten just until the screw is through the locknut.

9. Install GT2 pulley onto the stepper motor and attach the stepper motor to the X motor end using three M3x14mm screws.

10. Slide each 10mm smooth rod into one of the X ends, then slide X carriage onto rods, followed by the other X end.

Do not attach the timing belt yet (wait until you've mounted the X axis to the frame).

Parts needed:

Description | Quantity
X Idler end | 1
X Motor end | 1
X tensioner | 1
X Carriage | 1
Z Rack | 1
Z Pinion | 1
624 bearing belt guide (2 pieces) | 1
NEMA17 stepper motor | 1
GT2 timing pulley | 1
624 bearing | 1
Lead screw nut | 2
Endstop switch | 2
LM10UU linear bearing | 8
370mm 10mm smooth rod | 2
Miniature nylon zip ties (2mm width) | 6
M3 x 14mm screw | 7
M3 x 40mm screw | 1
M3 x 30mm screw | 1
M3 x 20mm screw | 1
M3 x 10mm screw | 2
M4 x 20mm screw | 2
M3 nex nut | 5
M3 locknut | 1
M4 locknut | 1
M4 hex nut | 1
0.625” extension spring | 2

Tools needed

Phillips screwdriver

Allen keys

Plier

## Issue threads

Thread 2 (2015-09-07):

Video build tutorial

WardBenjamin, 2015-09-07:
Hey Marty,

Do you have any plans to do something similar to what you did with the Wilson TS and make a series of build videos for this printer? It looks fairly similar, but there are a few major changes that could warrent some new videos.

WardBenjamin, 2015-09-07:
Welp. I just found your post about the W2 on reddit, I'll quote it here for anyone else who is interested.

> I won't have new assembly videos for a while, but if you've built the TS then you pretty much already know how to build this version too. (Marty Rice)

Closed 2015-09-07.

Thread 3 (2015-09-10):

Missing switch and leadscrew nut

timmit99, 2015-09-10:
The leadscrew nut and power switch are mussing from the BOM. These would be needed becaue the parts are designed to fit the specific ones you used.

Closed 2015-09-14.

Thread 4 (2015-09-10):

Missing switch and leadscrew nut

timmit99, 2015-09-10:
The leadscrew nut and power switch are mussing from the BOM. These would be needed becaue the parts are designed to fit the specific ones you used.

Closed 2015-09-10.

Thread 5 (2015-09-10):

Missing extruder fan duct

WardBenjamin, 2015-09-10:
When assembling a list of parts (by filename) to print based on the BOM, I found that you are missing the stl for the fan duct. I know there is one because there's one in the BOM as well as the picture on reddit, but apparently it didn't get added.

WardBenjamin, 2015-09-13:
I saw that you have added a fan duct specifically for the e3dlite6 hot end. Will this work for other hot ends, such as a hexagon or a jhead?

mjrice, 2015-12-12:
For the head hot end you would probably want to use the other fan duct which is located in the original Wilson repo in the stl/extruder folder. I am not sure which would work for a hexagon, it depends on the length.

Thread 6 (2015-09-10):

Make filenames exactly match BOM, or add filenames to the BOM

WardBenjamin, 2015-09-10:
When assembling the list of parts by filename that I need to print according to the BOM, I found that parts didn't exactly match. What I'm assuming is the Idler bearing guide is marked as a "belt-guide-624", which I only figured out because you use 624rs bearings. Also, some parts are not consistant with the rest, like "servo_mount" instead of "servo-mount" like it should be, and "z-motor-brace-1" and z-motor-brace-2" which are not marked in the BOM, instead it says to print 2 z motor braces and does not specify which files.

Basically, could you add the correct filenames to the BOM? Assuming you have printed the parts before it should be pretty easy.

WardBenjamin, 2015-09-13:
Thanks!

Closed 2015-09-13.

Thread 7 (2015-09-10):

No amount for Y tensioner part in BOM

WardBenjamin, 2015-09-10:
In the BOM, there is no amount in the "Printed Parts - Required"/"Quantity" section for the Y tensioner.

WardBenjamin, 2015-09-13:
Fixed, so closing.

Closed 2015-09-13.

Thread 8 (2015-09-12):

Z endtop

timmit99, 2015-09-12:
I noticed that the X-Motor has the adjustable screw for  the Z endstop but i don't see a Z endstop.stl. Is it the same as the Wilson V1 mount?

mjrice, 2015-09-12:
wilson2 is meant to use the servo-mounted endstop by default, so it doesn't need that one.  I didn't want to get rid of the adjustment screw mount on the X end however in case people want to use that instead of the servo for simplicity.  In that case, yes you'd just use the same endstop holder from wilson.

Closed 2015-09-14.

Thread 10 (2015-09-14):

Power Supply Mount

timmit99, 2015-09-14:
Would it be possible for there to be a CAD file for the Power supply? I like the ides of mounting it in the configuration as shown but i am using an ATX PC Supply and they are different sizes. I know i could model my own but i think an sCAD version of yours would be easily modifiable to any different supplies available.

mjrice, 2015-12-12:
The cad source for the power supply mount is in the Sketchup folder. It should be pretty simple to push the sides out to accommodate another form factor.

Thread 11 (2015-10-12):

Question about extruder filament path

ulmeck, 2015-10-12:
I noticed in the sketchup files, that if you create a cylinder flush with the hole right above the where the hotend goes, and extrude it towards the filament guide towards the top, it doesn't go straight through the model's filament path. This means that the filament come in through the guide, curves around the motor gear a bit, and then goes down the hole to the extruder at something of an angle. This is on all versions of the extruder back to mid 2014. I checked, and all parts of the extruder model are straight with the x/y axis of sketchup, just the holes are skewed.

Is there a reason for this? I would think that for more flexible filaments, a non-straight filament path would cause some problems, and in fact may have
caused a few problems for me printing with PETG filament (filament winding around the gear is a Bad Thing (tm)).

I've attached a picture of what I mean.

Thanks,

jf

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

tamarintech, 2016-01-06:
+1

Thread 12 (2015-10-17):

[Question] SCAD file of every part?

andreq, 2015-10-17:
I'm trying to make a Wilson 1.5 (mixing TS and 2 parts), but having a hard time using sketch up.
I do most of my design on Solidworks and OpenSCAD.

Is there plan to have SCAD file for all the parts?

mjrice, 2015-10-22:
I don't have any plans to re-design parts like the Y ends in scad.

andreq, 2015-10-22:
Thanks for the info.

I'm currently starting from scratch in Solidworks, I'll try to branch out from Wilson TS or host the file somewhere if I get anywhere with it.

I'm only looking to enhance the Z frame with the 2nd set of extrusion. It look way more solid on the Wilson 2 :).

Btw, thanks for designing those nice printer, I'm happy I chose the Wilson TS back in April!

Closed 2015-10-22.

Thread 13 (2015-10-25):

fixed z endstop stl missin

Arunk3001, 2015-10-25:
The stl for the z endstop from the Wilson ts design is missing from the stl folder. You mentioned in the Wilson 2 assembly video that you wanted to put that in the documentation.

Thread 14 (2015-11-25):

624rs bearing = 624-2rs?

tempestnano, 2015-11-25:
Should the bearing listed in the BOM as 624rs be 624-2RS? I was unable to find just a 624rs that wasn't just a cross-listed 624-2rs.

hasbridge, 2015-11-25:
I noticed the same thing, only the bearings I found are listed as 624ZZ. I think probably any "624" sized bearing would work.

mjrice, 2015-12-12:
@hasbridge is correct, any 624 bearing will work.

Closed 2015-12-12.

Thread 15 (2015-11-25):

Y ends have oversize holes for 10mm rods

hasbridge, 2015-11-25:
During assembly, I noticed that my 10mm rods are loose in the Y end pieces. I imported both STL files into sketchup, and each hole is oversized. On the y-motor stl, they appear to be 10.5mm, and on the y-idler piece, they appear to be 10.8.

thatch, 2015-12-26:
They are indeed oversized on the one I printed as well.  I'm switching to a more Taz-style Y end, as this piece is the toughest to print.

mjrice, 2015-12-26:
The idler end holes are indeed a little over sized, and I'll fix that tonight and push an update.  The .5mm on the motor end holes was intentional - with a 0.5mm nozzle, interior holes tend to be undersized by the diameter of the nozzle.  Maybe I should generate a couple different variations for smaller nozzles.

hasbridge, 2015-12-29:
I would actually prefer undersized by a tiny bit, because I could ream them with a 10mm drill bit to get a perfect 10mm hole afterwards.

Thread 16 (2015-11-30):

Im2596-mount.stl

feenix3k, 2015-11-30:
I tried to open the Im2596-mount.stl and got a error on the file. Slicer has been trying to repair it, but half of the image is missing when slic3r opens it to do repair.

Arunk3001, 2015-11-30:
I opened without a problem for me in both Cura and KISSlicer. Perhaps it's an issue with your downloaded copy or with slic3r. Try opening it with one of those programs if you can have them slice the model for you

Closed 2022-04-28.

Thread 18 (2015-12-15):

Issue slicing new z-lower-brace-1 and z-lower-brace-2

tamarintech, 2015-12-15:
When using Cura 15.02 to print the new lower braces they do not slice correctly.

z-lower-brace-1:
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

z-lower-brace-2 doesn't seem to load at all.  \* Edit: I just noticed that if you view it in the github viewer all of the faces are flipped.

z-lower-brace-pair loads correctly and slices as expected.

~~I'm not sure if this is a Cura issue or an issue with the Sketchup Exporter~~.  The STLs are weird.  I was able to print the braces after re-exporting them with Blender.  If other users experience the same issue I will gladly open a PR for the reexported braces.

Thanks!

thatch, 2015-12-26:
I have the same issue with Cura 15.04, including on z-brace-lower-pair.  I think it's mostly cosmetic, but it would be good to have a fixed version in the repo (either blender or netfabb exported).  (A friend doesn't see the error on his using s3d.)

thatch, 2015-12-26:
I checked and netfabb does not repair this issue, and neither do any of the "Fix horrible" expert options in Cura 15.04.  Can you open the PR?

Arunk3001, 2015-12-26:
I believe it's a issue with your settings in Cura. If you open the expert config window (MenuBar>Expert>open expert settings...) you should find in the lower right corner a section titled "Fix horrible". If I'm right, you have Combine everything(Type-B) selected. This setting fills in any gap between model walls, including space meant to be hollow. Try unchecking that setting and try slicing it again.

tamarintech, 2015-12-26:
Sorry, @Arunk3001 but please check the github viewer.  You'll find one of the braces actually has all of the faces flipped.

It looks like Marty pushed the braces through netfabb not long ago.  If that doesn't work for you then these are what I used:
https://github.com/tamarintech/Wilson2/blob/lower-braces/stl/z-lower-brace-1-reexport.stl
https://github.com/tamarintech/Wilson2/blob/lower-braces/stl/z-lower-brace-2-reexport.stl

Here's the most recent from Marty https://github.com/mjrice/Wilson2/commit/54ae108adc2ba3e7dde95da91132310c9987c57a

tamarintech, 2016-01-06:
I believe this is solved.
Closing.

Closed 2016-01-06.

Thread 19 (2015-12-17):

Orientation of PSU holder

tamarintech, 2015-12-17:
These should probably be flipped for easier printing.

tamarintech, 2016-01-03:
Resolved in https://github.com/mjrice/Wilson2/commit/7f1836028a587fb39719c86a27eca2cde187fa91

Closed 2016-01-03.

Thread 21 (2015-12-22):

Lead screw length is not a formula in the BOM

tamarintech, 2015-12-22:
I built to 400mm and seem to be needing 385mm lead screws.

Is Z height - 15mm a sane value for NEMA 17 with a coupler?

hasbridge, 2015-12-22:
My leadscrews (300mm) are about 20mm off the top of the motor mount - they don't need to go all the way down.

tamarintech, 2015-12-22:
You mean all the way down in the z-coupler?  Yea, I shoved mine all the way down.  I'd still end up with a pretty big gap.

What should the formula be?  Z - 15?  Z - 20?

hasbridge, 2015-12-22:
I am confused - are you saying your vertical extrusions are 400mm tall, or 400mm build height? For 400mm long extrusions (what I used), then 300 is the correct length for the lead screws. I would think the formula would always be Z - 100, with Z representing the total vertical extrusion length.

tamarintech, 2015-12-22:
Z rod: 400mm
Z axis extrusions (vertical frame piece in sheet): 480mm
Z Print height: 280mm

My lead screws are 350mm and 35mm away from the bearing trap - so that would mean I need 385mm lead screws.  480mm - 100mm sounds good - that would put me at 380mm which should fit in the bearing trap.

Should we get a note or a formula cell added to the sheet for Z axis extrusion - 100 = lead screw length?

Cell C19 would be =(C11-100) ?

hasbridge, 2015-12-22:
Yeah, I think that should work out correct. There should be a slight gap between the leadscrew and motor shaft inside the coupler, so that would account for the extra 5mm.

tamarintech, 2015-12-22:
https://github.com/mjrice/Wilson2/pull/23

E19 (lead screw length) updated to =C$11-(IF(B$3="metric",100,4)) where C11 is "Vertical frame piece" extrusion.

tamarintech, 2015-12-22:
Marty did it a bit more gracefully. ;)

https://github.com/mjrice/Wilson2/commit/cf690a2f3e09eeb61adfe3a06d8e54011543dffe

Closed 2015-12-22.

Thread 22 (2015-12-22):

Current xcarriage causes rod deflection, binding?

tamarintech, 2015-12-22:
Using the latest extruder (the closed-back version pushed November 9th) and LM10UU bearings I end up with 40mm rod-to-rod on one side of the xcarriage and 41mm rod-to-rod on the other side.

Maybe it's my material?  I'm using ABS.  The bearings might be deforming the xcarriage when I insert them.

tamarintech, 2016-01-11:
I'm going to assume this had something to do with material shrinkage or similar since it doesn't seem like anyone else has had the same experience.

Closed 2016-01-11.

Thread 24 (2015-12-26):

Z rods ~5mm too short

thatch, 2015-12-26:
Using the lengths from the BOM, and putting the z-motor parts against the table, the rods are about 5mm too short.  I can compensate for this by cutting them longer, it just seems like a doc problem.  Originally noticed by @precision with s3d and confirmed with my re-print using Cura.

mjrice, 2015-12-26:
The pocket on the top Z rod holders should have some room to spare with the 320mm smooth rod.  Either a few mm shorter or longer is meant to work.  Do you rods actually not reach the pocket?

precision, 2015-12-26:
Yeah, my right Z rod in particular was short and just barely reached the pocket.  I ended up sticking a M5 nut on top of the rod to snug up the fit.  Without the nut, it would wiggle itself out of the pocket. This is on Misumi cut extrusion and rods, btw.

mjrice, 2015-12-26:
Thanks for the feedback - I modified the z tops to extend the rod holder down another 5mm.

thatch, 2015-12-27:
Is your intention to make it so you can slip the rod into the top pocket while the printed parts are already on the extrusion?  If not, I think the top pocket needs to be at least 2mm shallower (and you can make the bottom one deeper by the same amount if you're concerned about fitting existing cut-too-long rods).

I measured mine today (not including your latest modification), and surface-to-surface is 310mm, bottom pocket is 4.7mm, top pocket is 11mm.  So with the rod pushed fully up, I have 1mm gap at the bottom.

thatch, 2017-10-18:
I'm no longer building a Wilson2, so closing.

Closed 2017-10-18.

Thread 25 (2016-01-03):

MDF Print Deck 200x300 heated bed

tempestnano, 2016-01-03:
For the laser-cut bed design in wilson-bed-2030-lc.svg, the mounting holes corospond exactly to an 8.4"x12.6" heated bed, but are slightly too small for a 300mmx200mm heated bed as called for in the BOM.

I would propose either calling for an 8.4x12.6 heated bed in the bom, or specify that the laser-cut design requires modification for a 300x200 bed.

Algram, 2016-02-19:
+1 on this. Especially since it is very hard to get a 314x214 heated bed on aliexpress.

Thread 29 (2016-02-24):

Missing screw/nut from BOM

hopping-cricket, 2016-02-24:
It seems like the 4mm screw/lock nut for the guidler bearing is missing from the BOM.

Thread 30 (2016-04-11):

Loose fitting x pieces

tbd-develop, 2016-04-11:
I've printed the x end-stops and when I go to put the bearings in there they are extremely loose. The x-carriage printed with the same settings, the same bearings are tight so I don't understand what I'm doing wrongly. I am printing at 25% infill with a .15 layer height, 4 top/bottom layers and 3 perimeters.

ShRTee, 2016-08-02:
I did mine an they were fine, but now i have done these: http://www.thingiverse.com/thing:1201566
It seems that the bearings and the rods are loose, thay are not as tight as the original parts.
What am i doing wrong ??
printing in a Wanhao 4S with 3 laysers shell and 50 % infill.
Done them twice now, but same result

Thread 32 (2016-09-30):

Error in Z calculation - Wilson II BOM

WZ9V, 2016-09-30:
Cell C17 is missing formula "=ROUND(IF(B$3="metric",E17,E17/25.4),1)" so Z extrusion size never changes because its always 320mm

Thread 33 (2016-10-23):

Modify parts to use 8mm Smooth Rod

iguanahotsauce, 2016-10-23:
Would it be possibly to modify the parts that use the 10mm smooth rods to take 8mm smooth rods instead?

I already have a large amount of 8mm smooth rod left over from my last two printer builds and I do not have any 10mm smooth rods so I would need to go purchase them. I know the printer will be better with 10mm smooth rods but for now using the 8mm smooth rods I already have would be best.

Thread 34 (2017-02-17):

Parametric Parts List needs modifying for rack & pinion flip down Z-probe

dtbee, 2017-02-17:
I have built a **Wilson II** for a **_300mm L x 300mm W x 250mm H_** build area based upon the part dimensions provided by the parametric parts list.  The X-axis only provides a useable width of _**286mm**_ and this seems to be due to the revised Z probe mechanism.

The useable width measurement was obtained by measuring the travel of the extruder carriage from the point where the Z-probe rack is just touching the X-end motor striker plate (but not extending the probe) and the point where the Z-probe rack is just touching the X-end idler striker plate (but not retracting the probe).

Adding a constant of **15mm** to the X-axis calculations for the extrusions and smooth rods lengths would resolve this issue.

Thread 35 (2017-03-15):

Coupler 5x8 removed?

damccull, 2017-03-15:
In commit 7a973b5f5a37ae7db1a1cd6b9108b6ed6812ef87 the coupler-5x8.stl file was removed. Is this intentional, and would I need this file in order to build the Wilson II?

timmit99, 2017-03-16:
I built my Wilson II a while back and have just been using a spiral cut shaft coupler like [this](https://www.amazon.com/OctagonStar-Flexible-Couplings-Printer-Machine-2PCS/dp/B01HBPHSII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) They have worked great for my Wilson II as it is the workhorse of my 4 printers right now.

Closed 2021-06-29.

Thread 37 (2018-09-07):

Holes in bottom on Y motor/idler

timmit99, 2018-09-07:
What are the holes in the bottom of the Y-Ends for? If they are for mounting the printer down to a baseplate how are they designed to be used/what is the proper method for using them?
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

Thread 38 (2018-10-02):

Tensioner bad bore

mexbravo, 2018-10-02:
the new design of the tensioner (x andY) is 3mm, and bore of 624RS Bearing is 4mm

mexbravo, 2018-10-02:
I undestand now,I need to use  this one

https://www.banggood.com/3pcs-16T-GT2-Aluminum-Timing-Pulley-With-Tooth-For-DIY-3D-Printer-p-1339218.html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

or

https://www.banggood.com/5pcs-16T-Aluminum-Timing-Pulley-Without-Tooth-For-DIY-3D-Printer-p-1339225.html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

update de BOM

Regards

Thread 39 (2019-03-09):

error firmware

Rosuu, 2019-03-09:
'MYSERIAL' was not declared in this scope marlin
please help me..i have this error

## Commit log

2015-09-07 Wilson II initial commit
    [filament-mount.stl, power-switch-mount.stl, psu-mount.stl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]
2015-09-07 remaining stls, extruder files, and a bom
    [belt-guide-624.stl, extruder-direct-drive.skp, extruder-direct-drive.stl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]
2015-09-08 x-tensioner and bom update
    [extruder-direct-drive.skp, wilson-ii-bom.ods, x-tensioner.stl]
2015-09-08 a tweak of the x tensioner for fit
    [x-tensioner.stl]
2015-09-10 adding fan duct
    [FanductOvalE3dv6.scad, fan_holder_v2.scad, shapes.scad]
2015-09-12 updates to bom
    [wilson-ii-bom.ods, x-tensioner.stl]
2015-09-12 more bom update
    [wilson-ii-bom.ods]
2015-09-30 drawing of how to cut the mdf print deck
2015-10-12 added laser cut bed design and update to ztops
    [z-top-left.stl, z-top-right.stl]
2015-10-31 add lm2596 dc:dc converter mount
    [lm2596-mount.stl]
2015-11-10 updated x-carriage
    the top of the belt holders on the X carriage were raised by 4mm, which
    makes the belt more parallel with the top of the X idler belt guide. an
    image of it is included in doc/
    [wilson-ii-bom.ods, x-carriage.stl]
2015-11-14 fixed some mesh errors in the y motor and idler models
    [y-idler.stl, y-motor.stl]
2015-12-12 beefed up lower z brackets, added holes to the LM2596 mount for alternate PCB, thickened X tensioner yoke
    [lm2596-mount.stl, x-tensioner.stl, z-lower-brace-1.stl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]
2015-12-19 added detailed images for 3-prong power switch wiring
2015-12-20 added some room in the power switch mount for connectors; turned power supply mount over for easier printing
    [power-switch-mount.stl, psu-mount.stl]
2015-12-22 added a formula for the threaded rod length to the bom spreadsheet
    [wilson-ii-bom.ods]
2015-12-26 Y idler end rod holes shrunk by .4mm, lower z braces put through netfabb
    [y-idler.stl, z-lower-brace-1.stl, z-lower-brace-2.stl]
2015-12-26 extended rod holder on z-top pieces by 5mm
    [z-top-left.stl, z-top-right.stl]
2015-12-31 fixed a thickness error on the psu mount bracket, added beveled lower corners to y-brace, and rod clearance for y-table
    [extruder-direct-drive-3mmbody.stl, extruder-direct-drive.skp, psu-mount.stl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]
2016-01-07 fixed missing slots on ramps mount
    [ramps-mount.stl]
2016-01-24 added a minimalist fan shroud, and an alternate servo mount that works better for some.
    [extruder-direct-drive.skp, fanduct-minimalist.stl, servo_mount.skp]
2016-01-26 tweak to extruder body
    fixed ~1mm slope in extruder feed tube, extended 1mm toward drive gear
    for more support for flex filament, and added 1.75 emboss mark to the
    body.
    [extruder-direct-drive.skp, extruder-direct-drive.stl]
2016-02-07 Added an alternate fan duct for e3d hot ends
    [fanduct-e3dlite6-alt.stl]
2016-02-21 Added models for Z rack & pinion bed probing mechanism
    details about this update are at
    http://community.reprapwilson3d.com/t/a-new-way-to-probe-the-print-bed-bed-leveling
    [configuration.scad, x-carriage.stl, x-end-idler.stl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]
2016-02-21 moved zip tie holder on new x carriage to a better spot
    [x-carriage.stl]
2016-02-22 tweak of wire guide on x-carriage and length of z-rack
    [x-carriage.stl, z-rack.stl]
2016-02-23 fixed a model error in the x-carriage and improved z-pinion with endstop blocking ridge and ziptie mount
    [x-carriage.stl, z-pinion.stl]
2016-03-05 added wider xy tensioners for delrin or aluminum idler pulleys
    [xy-tensioners-wide.skp, xy-tensioners-wide.stl]
2016-03-05 some reorganization of files
    [extruder-direct-drive-3mmbody.stl, extruder-direct-drive.stl, fanduct-conical.stl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]
2016-03-19 new tensioners for 3mm bore idlers
    [x-tensioner-3mm.stl, y-tensioner-3mm.stl]
2016-03-27 new PSU mount with IEC receptacle
    [psu-mount-bottom.stl, psu-mount.stl, psu-mounts.skp]
2016-04-06 moved axis of x tensioner 3mm bore idler pulley 2mm
    [x-tensioner-3mm.stl]
2016-04-30 tightened up a few loose fittings and added pica board mount
    [pica-mount.stl, x-end-idler.stl, x-end-motor.stl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]
2016-05-15 added printable shaft coupler and some doc images
    [coupler-5x8.skp, coupler-5x8.stl, extruder-direct-drive-3mm.stl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]
2016-05-24 beefed up some parts for strength (y-idler, z motors) and tweaked y-table for belt offset
    [5df-holder.skp, coupler-5x8.skp, rack.stl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]
2016-06-05 refactored sketchup models so that each part has it's own sketchup file, moved others to a subfolder
    [5df-holder.skp, coupler-5x8.stl, extruder_body.skp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]
2016-06-18 fixed tensioner hole spacings
    [x-tensioner.stl, x_tensioner.skp, y-tensioner.stl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]
2017-01-27 Revised X & Y tensioners for improved strength
    [x-tensioner.stl, x_tensioner.skp, y-tensioner.stl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]
2020-04-25 add power inlet detail photos
    [coupler-5x8.skp, coupler-5x8.stl, extruder-clamp.stl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]
